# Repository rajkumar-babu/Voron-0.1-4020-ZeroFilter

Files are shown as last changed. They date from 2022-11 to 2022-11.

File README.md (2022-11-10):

# Voron-0.1-4020-Zerofilter
A Zerofilter Mod for the Voron 0.1 with a 4020 blower.



This Mod uses a 4020 Blower fan instead of a 4010 to increase the airflow on the [zruncho's *Zerofilter*](https://github.com/zruncho3d/zerofilter) for the Voron 0.1. The aim is to use the cartridge for ABS printing and interchange it with a [Vez3D RSCS](https://github.com/VzBoT3D/VzBoT-Vz235/tree/main/Assemblies%20%26%20STL/RSCS) style duct for PLA printing. The inspiration was from the idea proposed by *Dingushippo#6564* on Discord to have interchangeable Cartridge and Airduct. The **Side Mount** used in this mod was inspired by [Revnull's *voron_v0.1_side_mount*](https://github.com/revnull-src/zerofilter/tree/main/Mods/revnull/voron_v0.1_side_mount).

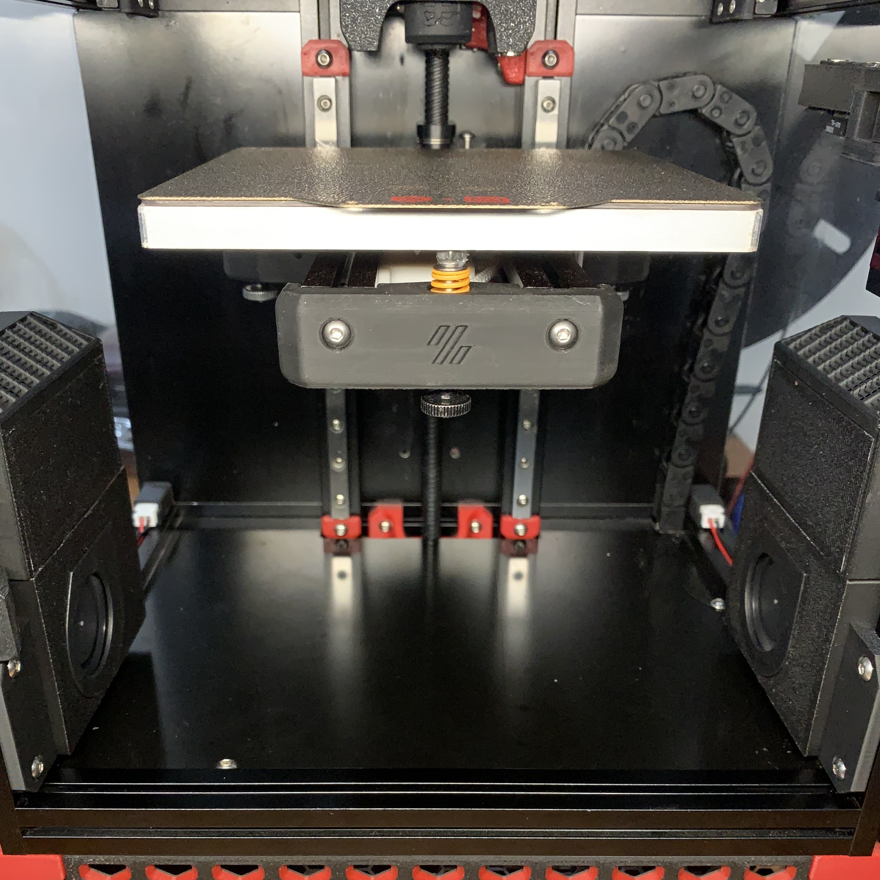
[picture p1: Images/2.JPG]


# Parts to print
  * Core L ×1
  * Core R ×1
  * Lid L ×1
  * Lid R ×1
  * Side Mount L ×1
  * Side Mount R ×1

The parts are marked L and R for left and Right sides respectively and are properly oriented for printing.
  
# Print settings
  I followed the standard Voron print settings.
  * Material - ABS
  * 0.2mm layer height
  * 5 top and bottom layers
  * 4 perimeters
  * 40% infill
  * Forced 0.4mm width.

# BOM
  * Printed parts
  * 4020 Ball Bearing Blower Fans ×2
  * M3×6mm BHCS ×4
  * M3x8mm BHCS x4
  * M3×16mm BHCS x4
  * M3 Hex Nut ×4
  * M3 Heat Set Insert (M3×5mm×4mm) ×8
  * JST XH crimp terminals ×4
    * Or Microfit or JST PH or Ferrules as required for your setup.
  * JST XH 2 pin plug (Optional)
    * Can be reused from the fans.
  * 6mm×3mm Magnets ×8
    * Can get away with ×4 magnets as well.
  * Cartridge assembled and filled with carbon.
  
# Assembly Instructions

**STEP 1.**

Install the ×2 Heat Set Inserts on the inside of **Core** for mounting the fans. Be careful not to touch the narrow walls with the soldering iron. I used an LDO heatset installion tip and had enough clearance.

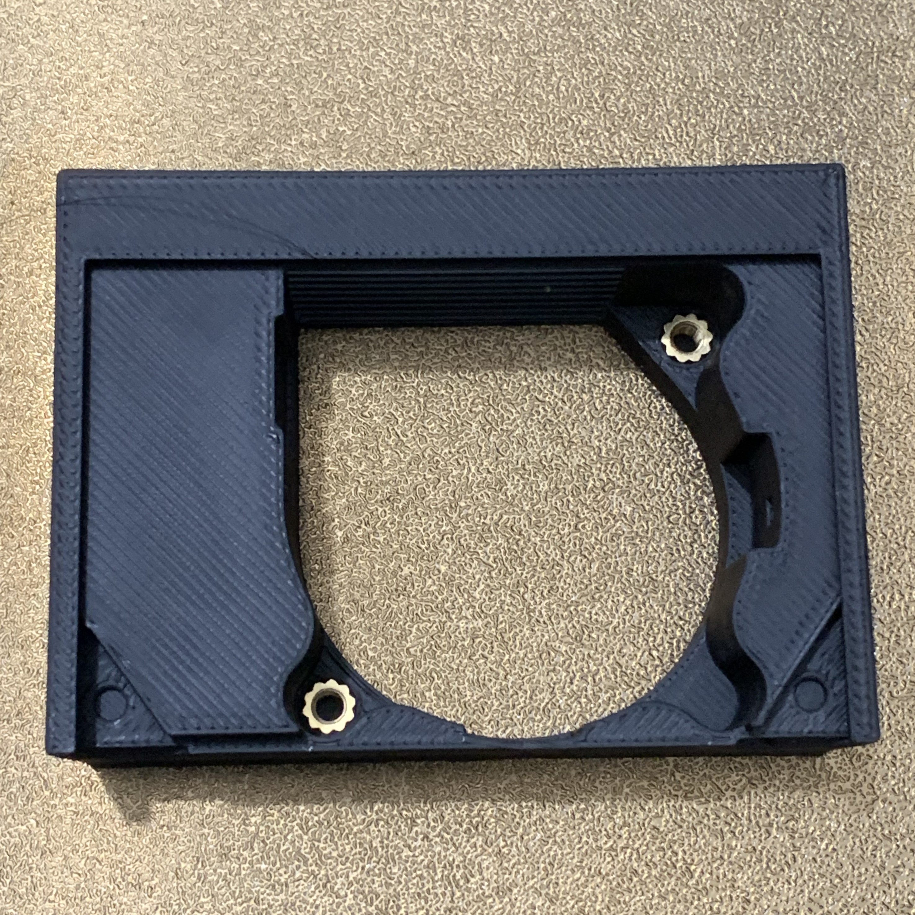
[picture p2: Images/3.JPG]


**STEP 2.**

Install the ×2 Heat Set Inserts on the inside of **Core** for mounting the **Side Mount**

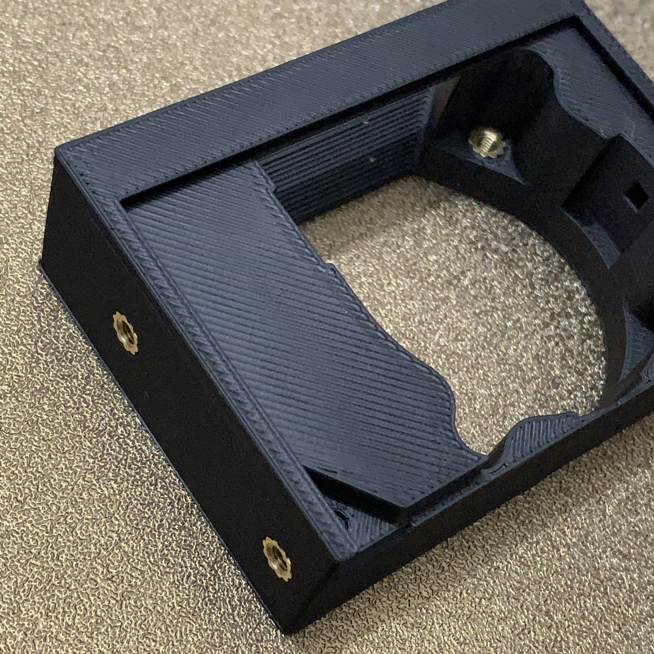
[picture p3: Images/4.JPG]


**STEP 3.**

If your fan wires has a connector at the end remove the connector and snip the crimp terminals. Make sure you leave the wires as long as possible which aids in installation and can be trimmed later. This is essential to feed the wire through the channel.
Feed the wire through the slot on the inside of the **Core** and it should come out on the bottom.

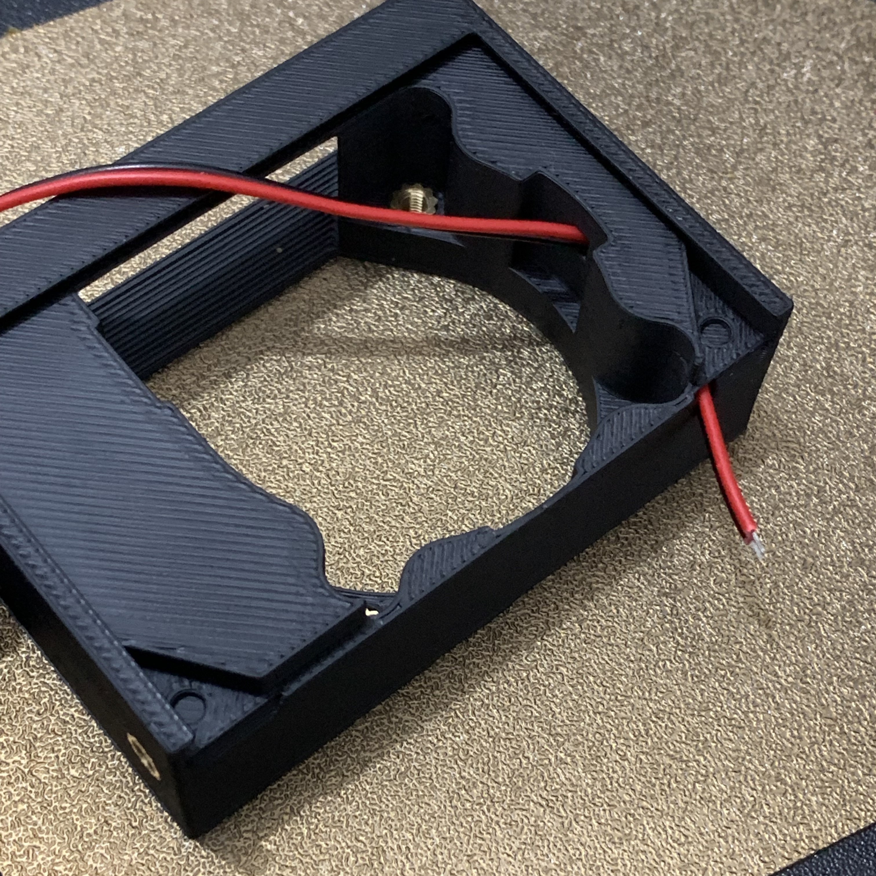
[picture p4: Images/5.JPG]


**STEP 4.**

Gently Pull the fan wires out of the channel and guide the fans into the **Core** at the same time pushing it down. The fan orientation should not be an issue as it would go in all the way in only one direction. The channels are oversized and you shouldn't feel any resistance. If there is any resistance pull the wires slightly back and feed them again. The wires should sit flush to the top surface, not to interfere with the **Lid**

**STEP 5.**

Fasten the fan to the **Core** with x2 M3×16mm BHCS. Do not worry about the bolt heads sticking out. The **Lid** has enough clerance and would not hit or cause any binding as long as the bolts are ISO 7380-1. 

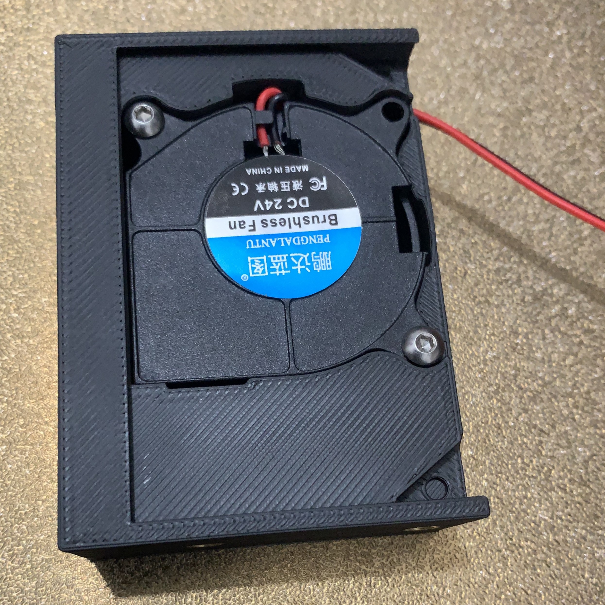
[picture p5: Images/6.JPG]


**STEP 6.**

Fasten the **Side Mount** to the **Core** using x2 M3×6mm BHCS.

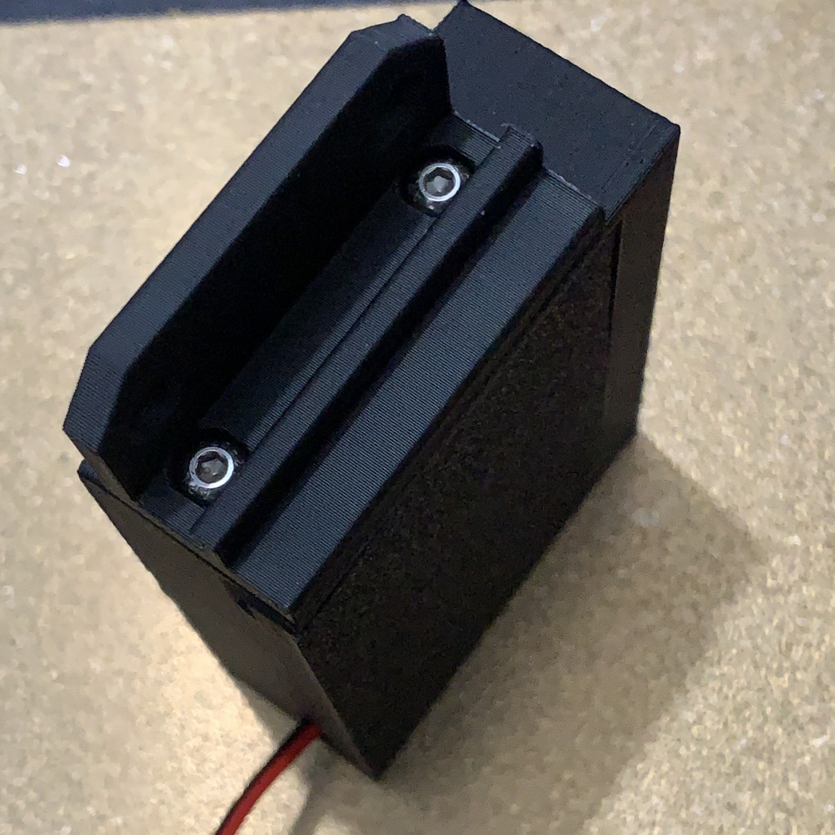
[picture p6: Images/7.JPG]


**NEXT STEPS**

The next steps are
1. Install the magnets as per the [Zerofilter's guide](https://github.com/zruncho3d/zerofilter#assembly-instructions). Make sure the polarity matches with the corresponding Left and Right Cartridge.
2. Slide the **Lid**. The **Lid** is a remix of the [Zerofilter's Lid](https://github.com/zruncho3d/zerofilter#design-details) that attaches using a detent. There are notches at the bottom of the **Core** to remove the **Lid** if required. Take a note on the L and R markers on the **Lid** and intall it to their corresponding sides as they have intends to clear the rear M3 bolt heads.
3. Mark the length of wire required to connect the fan to the MCU or [Klipper Expander](https://github.com/VoronDesign/Voron-Hardware/tree/master/Klipper_Expander), cut to length, strip, crimp the terminals and plug them to your board. Follow [Zerofilter's Config](https://github.com/revnull-src/zerofilter#software-config) to setup the fans.
4. I used Revnull's [1515 Snap-in Mount](https://www.printables.com/model/163116-2-pin-jst-hx-1515-snap-in-mount) for the JST connectors inside the chamber for earier maintenance.

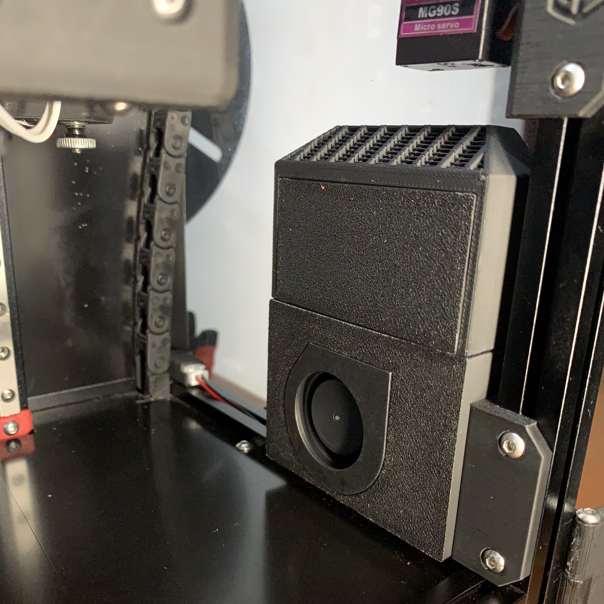
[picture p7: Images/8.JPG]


5. Mount the **Core** assembly to the frame as per [voron_v0.1_side_mount](https://github.com/revnull-src/zerofilter/tree/main/Mods/revnull/voron_v0.1_side_mount) or [Side Swipe](https://github.com/oldfar-t/Side-Swipe-Magnetic-Probe) or [Slide Swipe](https://github.com/chestwood96/SlideSwipe) instructions.
5. Attach the cartridge and start printing.

# What's next?

To design and test an [Vez3D RSCS](https://github.com/VzBoT3D/VzBoT-Vz235/tree/main/Assemblies%20%26%20STL/RSCS) style duct.

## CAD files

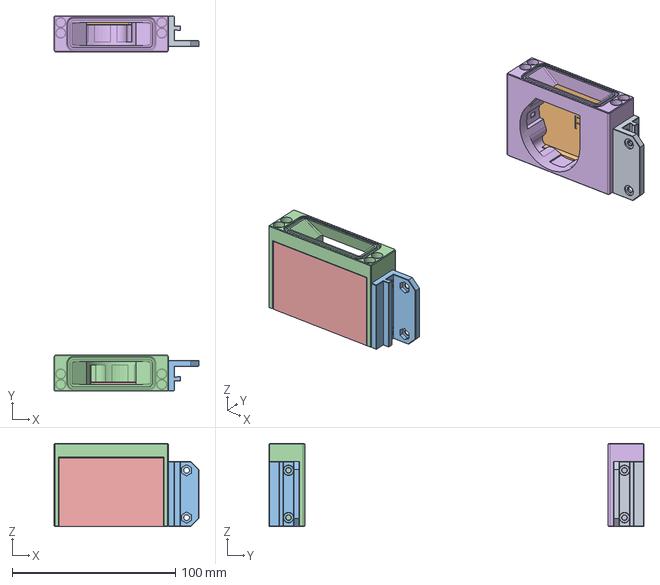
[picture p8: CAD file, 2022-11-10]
CAD/ZeroFilter 4020 Mod.step
88.7 x 230.0 x 51.0 mm

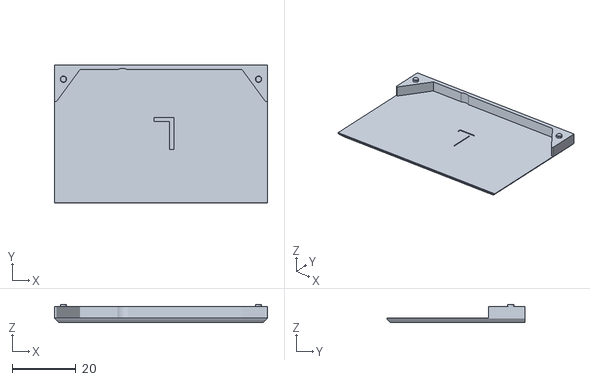
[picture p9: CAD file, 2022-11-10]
STLs/Lid L.stl
66.6 x 43.3 x 5.75

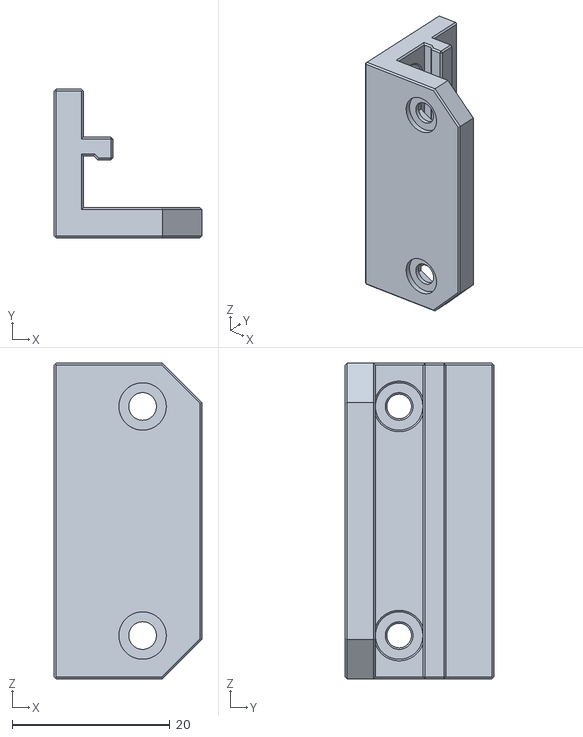
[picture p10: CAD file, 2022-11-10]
STLs/Side Mount R.stl
18.7 x 18.8 x 40.0

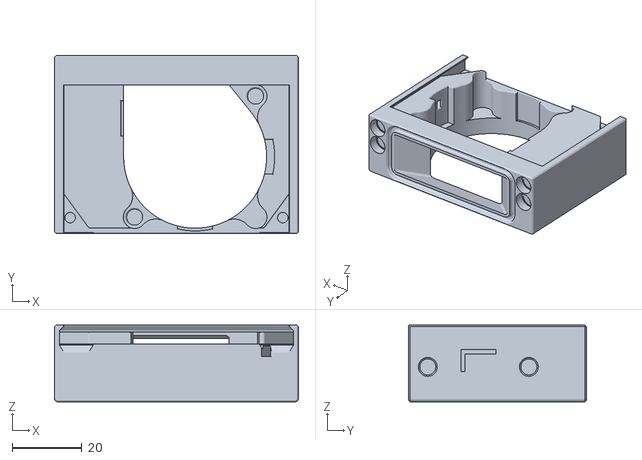
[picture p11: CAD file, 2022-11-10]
STLs/Core L.stl
70.0 x 51.0 x 22.0

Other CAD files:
STLs/Lid R.stl
STLs/Core R.stl
STLs/Side Mount L.stl
CAD/ZeroFilter 4020 Mod.f3d

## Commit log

2022-11-10 Create CAD
2022-11-10 Create Stl
